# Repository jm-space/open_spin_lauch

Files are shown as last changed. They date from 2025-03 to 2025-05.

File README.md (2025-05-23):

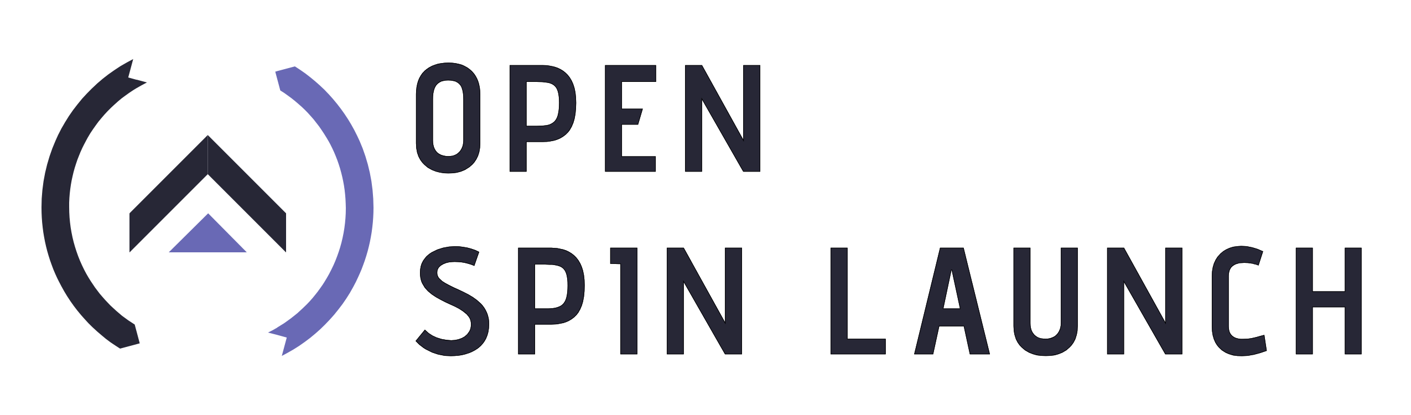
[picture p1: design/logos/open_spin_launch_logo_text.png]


------------------------------------------------

A spin launch system that will be used as the launch platform for many of our future projects. Probable missions that could be conducted with this launch platform include

- Deploy and propulsive landing
- Deploy and in-flight stage ignition
- Deploy to UAV flight transition

The system's main objective is to support the goal of a propulsive landing by accurately deploying it to a target altitude. 

## Requirements

### Spin Launcher

- Maximum achievable altitude: 150 m (theoretical altitude - drag not included)
- Maximum radius: 2 m
- Maximum rocket weight: 2 kg
- Spin up mechanism: 
the contraption should be built in a way so that it can either be spun up  (i) manually with human power through cycling or (ii) with the help of an asynchronous electric motor. 
For human cycling power, a maximum of 800 W is assumed for a maximum duration of 30 s.
- Spin-up retrofit: initially method (i) will be installed. However, method (ii) should be easily installable without any changes. In addition, a clutch should allow for seamless switching between the two modes. 
- Release mechanism: (i) must be able to release two attachment points at specific times, (ii) the release mechanism must be able to deploy the vehicle with a directional accuracy of 1°, which results in a landing zone deviation of +-10 m when launched to the absolute maximum altitude of 150 m with target direction 3°. (iii) The timing accuracy of the differential release mechanism must be high enough, such that if a remaining rotation is induced by the inaccuracy of the differential release, the fins are able to keep the altitude loss and trajectory deviation sufficiently small. 
- Counterweight: instead of utilizing a counterweight, a second (decoy) rocket should be attached that will be released in the same launch direction with a time offset of half a rotation. The axle should be able to withstand the half-rotation induced imbalance. 
- Frame structure: will be made of rectangular steel tubes that will be connected by welding.
- Movability: the contraption should be built on a movable platform for easy commuting. In addition, the platform could be powered by the integrated cycle.  
- Modularity: the individual components of the spin launcher should be split into modules to allow for easy replacements and upgrades. In addition, the entire spin launch system should be able to be retrofitted into a bus without much additional effort. 
- Video coverage: a camera should be installed in the spin launcher's arm so that it can capture the differential release of the vehicle. 

### Rocket

Requirements and expected feature changes:

- Structural integrity: the rocket must be able to withstand the highest occurring launch g-forces. 
- Attachment points: the rocket should integrate two attachment points with which it can be connected to the spin launcher. Those attachment points should be high-strength, durable, and should allow for rapid reuse. 
- Fins and COG: the rocket will have the landing engines and most of its weight in its front and fins in its rear, which allow for a passively stabilized launch. After reaching apogee, the rocket will flip into its stable descent orientation, with its fins being on top and the engine pointing downwards. 
- Thrust vector control: (i) the new TVC system should use off-the shelf gears for higher precision. (ii) it should utilize KST servos for faster actuation speeds and higher accuracy. (iii) and it should be available in two configurations - one for our self-developed solid rocket engines and one for a set of up to five Klima Raketenmodellbau engines. (iv) a life thrust measuring system should be incorporated into the new TVC system. 
- Solid rocket engines: over the course of this vehicle's development several types of engines should be devised: (i) a long-burning engine primarily used for landing maneuvers (ii) a high thrust engine for in-flight ignition, and (iii) a long burn time medium thrust version for rocket powered UAV flight.  
- Throttle mechanism: some mechanism should be devise that allows for sufficient throttle control to increase the likelihood of a successful landing. 
- GNSS receiver: for position and velocity determination a RTK GNSS receiver should be incorporated. 
- Video coverage: two cameras should be installed in the vehicle - one that is directed towards the TVC system and one that is filming the vehicle's exterior.

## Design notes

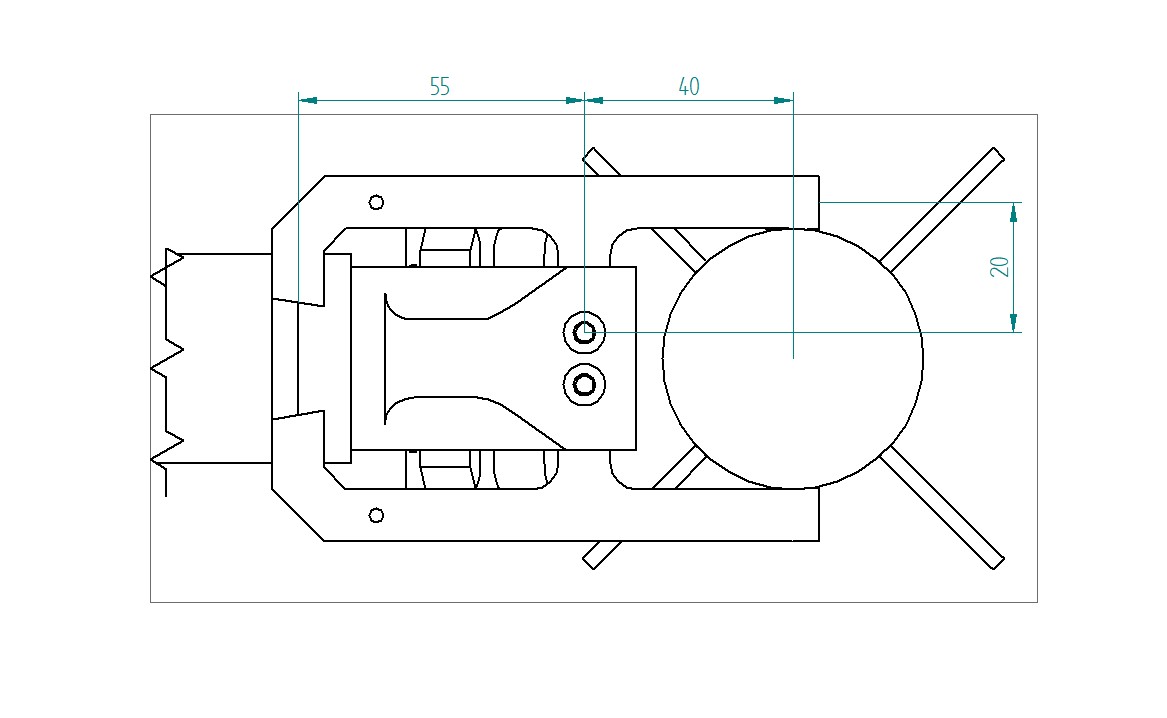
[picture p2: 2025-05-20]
documents/calculations/FBD1-clamp.jpg

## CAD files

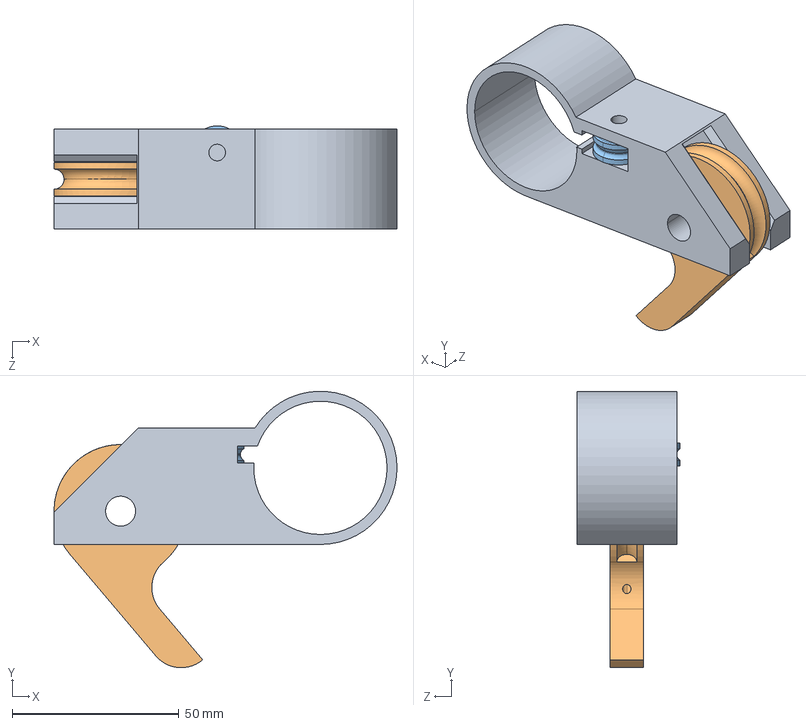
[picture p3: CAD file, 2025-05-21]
construction/prototype_v2/main_trigger.STEP
103.0 x 83.0 x 31.0 mm
housing
lever

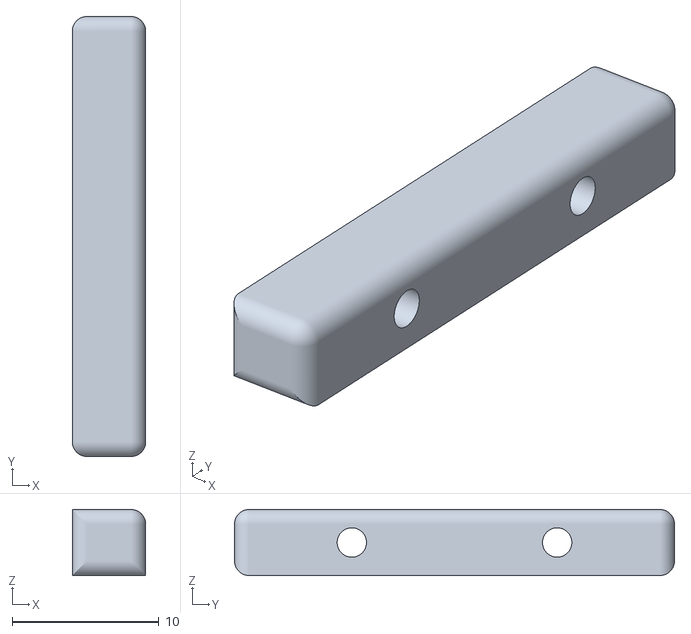
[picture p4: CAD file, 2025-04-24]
construction/small-scale_prototype/a1_front_release_mechanism/stl/upper_clamp_release_pin.stl
5.00 x 30.0 x 4.50

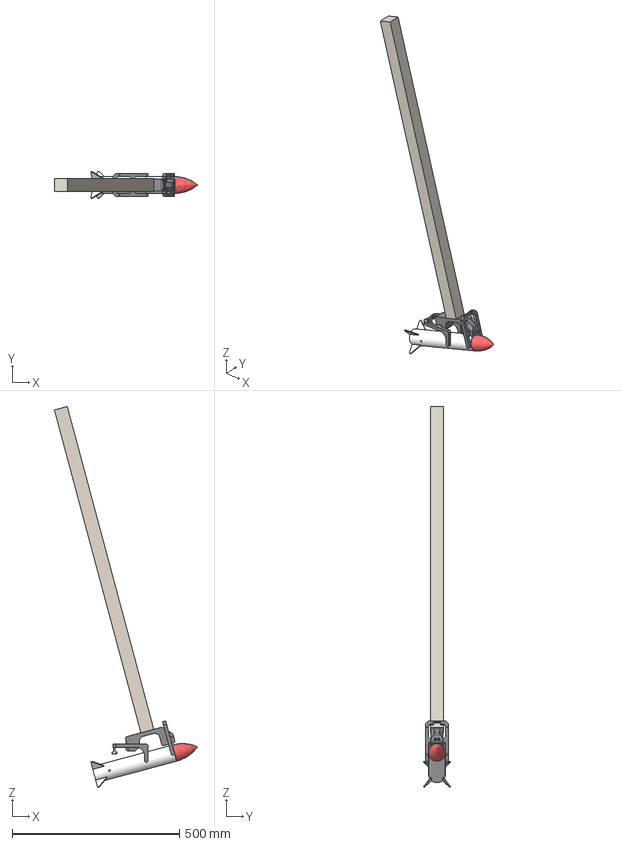
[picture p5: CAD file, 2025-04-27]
construction/small-scale_prototype/a2_auto_release_mechanism/a2_release_mechanism.stp
428.6 x 81.0 x 1140.0 mm
rod_endpart
rocket_dummy
upper_rocket_clamp_left
a1_upper_rocket_clamp_left
upper_rocket_clamp_right
a1_upper_rocket_clamp_right
upper_clamp_release_pin
a1_upper_clamp_release_pin
rocket_dummy_nose_cone
attachment_wood_plank

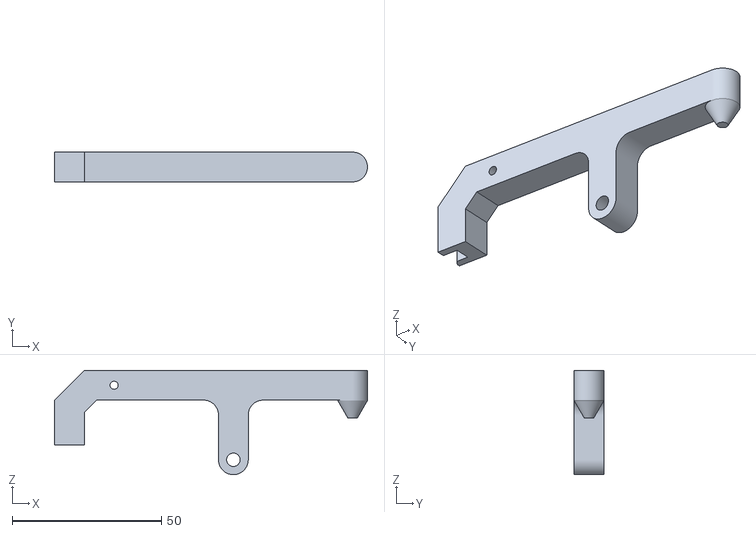
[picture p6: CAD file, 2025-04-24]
construction/small-scale_prototype/a2_auto_release_mechanism/stl/upper_rocket_clamp_left.stl
105.0 x 10.0 x 35.0

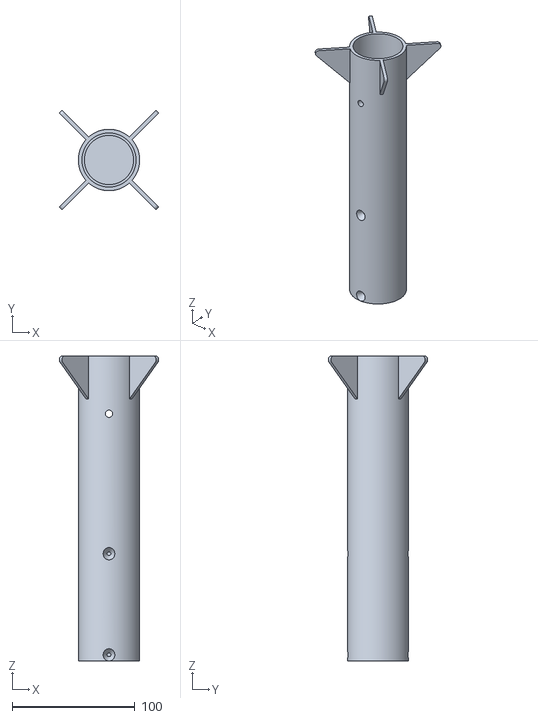
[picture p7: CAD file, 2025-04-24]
construction/small-scale_prototype/a2_auto_release_mechanism/stl_2/rocket_dummy.stl
81.0 x 81.0 x 248.3

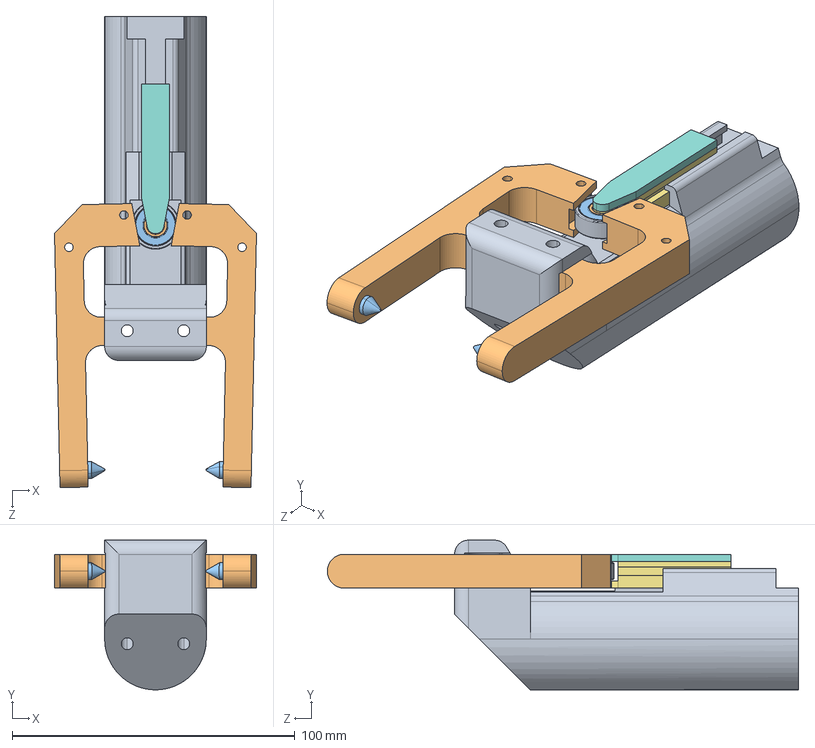
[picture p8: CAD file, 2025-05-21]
construction/prototype_v2/front_release.STEP
71.5 x 53.0 x 166.8 mm
front_endpart
front_clamp_left_b x 2
din8012 x 2
skf_bearing_hk_0306_tn_2_01 x 2
skf_bearing_hk_0306_tn_2_02 x 2
skf_bearing_hk_0306_tn_2_03 x 2
release_pin_lower
release_pin_upper
w_606-2rs1_01
w_606-2rs1_02
w_606-2rs1_03
w_606-2rs1_04
w_606-2rs1_05

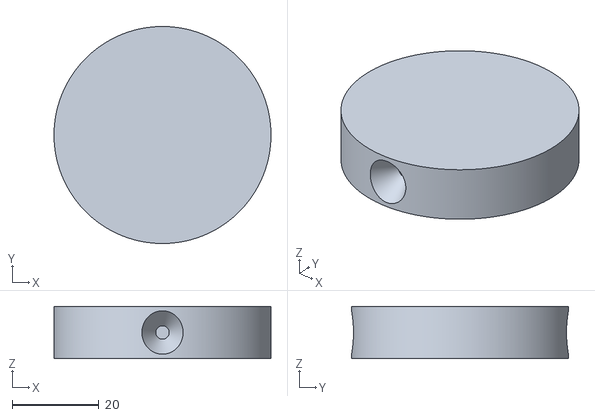
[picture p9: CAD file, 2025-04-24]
construction/small-scale_prototype/a2_auto_release_mechanism/stl/rocket_dummy.stl
50.0 x 50.0 x 12.0

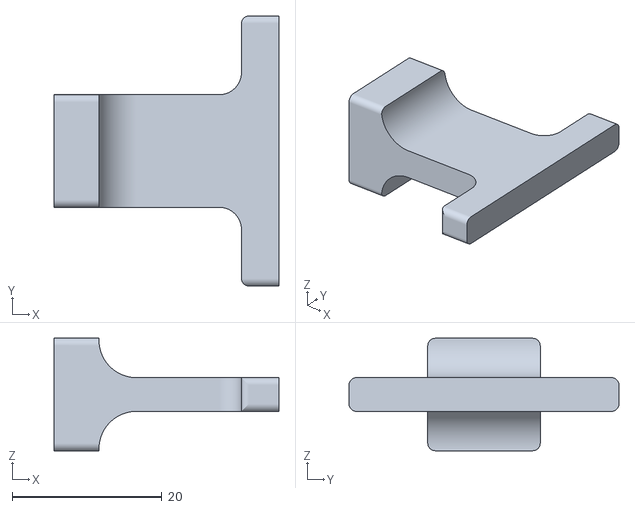
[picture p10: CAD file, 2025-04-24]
construction/small-scale_prototype/a2_auto_release_mechanism/stl_2/upper_clamp_release_pin.stl
30.0 x 36.0 x 15.0

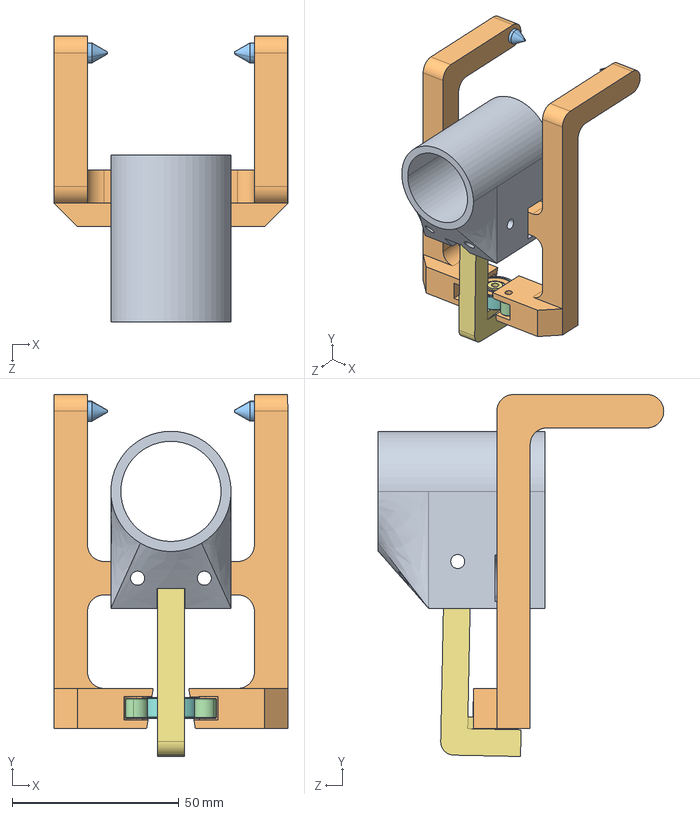
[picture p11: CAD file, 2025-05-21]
construction/prototype_v2/rear_release.STEP
70.0 x 108.4 x 85.5 mm
rear_endpart
rear_clamp_left_b
din8012 x 2
skf_bearing_hk_0306_tn_2_01 x 2
skf_bearing_hk_0306_tn_2_02 x 2
skf_bearing_hk_0306_tn_2_03 x 2
rear_clamp_right_b
swing_b
w_606-2rs1_01
w_606-2rs1_02
w_606-2rs1_03
w_606-2rs1_04
w_606-2rs1_05

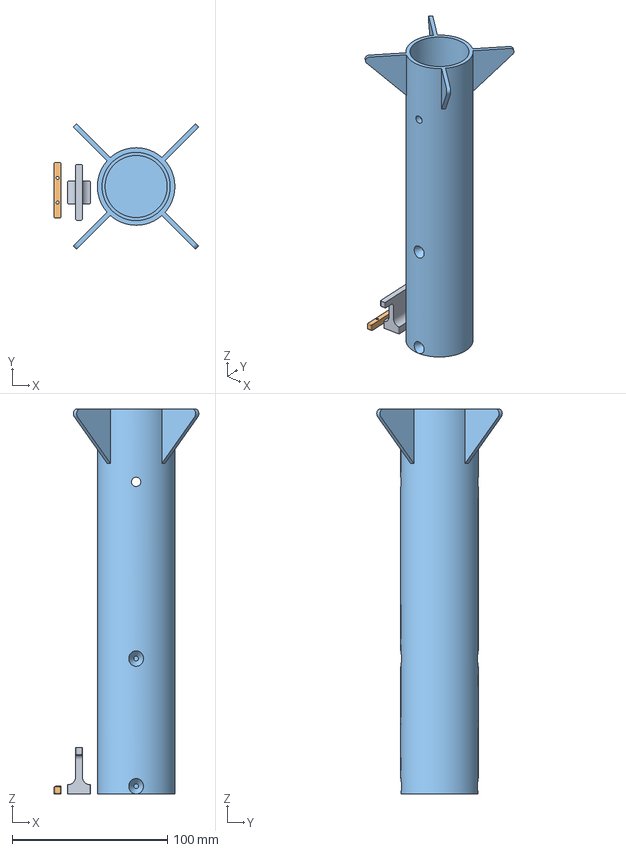
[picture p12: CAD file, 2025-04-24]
construction/small-scale_prototype/a2_auto_release_mechanism/stl_2/a1_upper_clamp_release_pin.3mf
93.4 x 81.0 x 248.4 mm
upper_clamp_release_pin.stl
a1_upper_clamp_release_pin.stl
rocket_dummy.stl

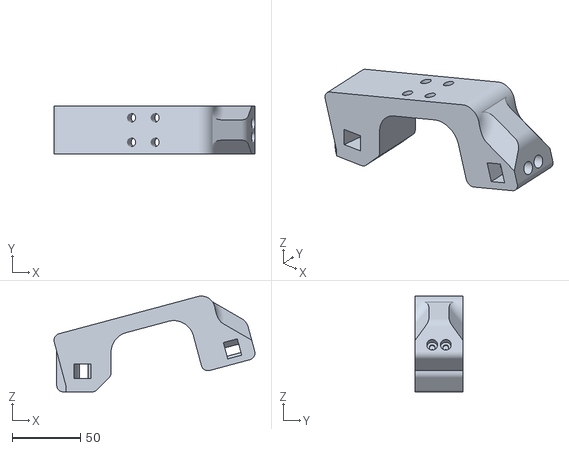
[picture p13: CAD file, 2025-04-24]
construction/small-scale_prototype/a2_auto_release_mechanism/stl_2/rod_endpart.stl
147.7 x 35.0 x 70.4

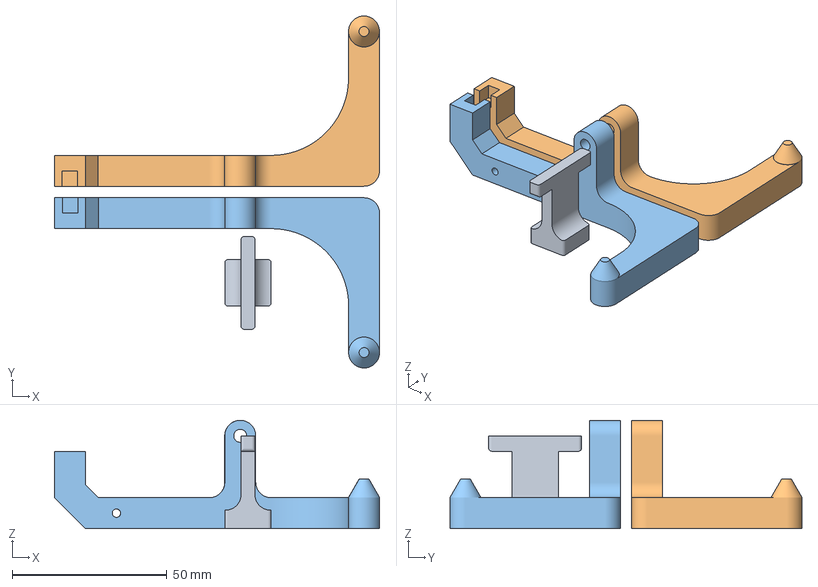
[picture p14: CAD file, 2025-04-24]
construction/small-scale_prototype/a2_auto_release_mechanism/stl_2/upper_rocket_clamp_left.3mf
105.0 x 113.7 x 35.0 mm
upper_clamp_release_pin.stl
upper_rocket_clamp_left.stl
upper_rocket_clamp_right.stl

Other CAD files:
construction/small-scale_prototype/a1_front_release_mechanism/stl/upper_rocket_clamp_right.stl
construction/small-scale_prototype/a2_auto_release_mechanism/stl/upper_rocket_clamp_right.stl
construction/small-scale_prototype/a2_auto_release_mechanism/stl_2/a1_upper_rocket_clamp_right.stl
construction/small-scale_prototype/a2_auto_release_mechanism/stl_2/a1_upper_clamp_release_pin.stl
construction/small-scale_prototype/a2_auto_release_mechanism/stl_2/a1_upper_rocket_clamp_left.stl
construction/small-scale_prototype/a2_auto_release_mechanism/stl_2/rocket_dummy_nose_cone.3mf
construction/small-scale_prototype/a2_auto_release_mechanism/stl_2/upper_rocket_clamp_left.stl
construction/small-scale_prototype/a2_auto_release_mechanism/stl_2/upper_rocket_clamp_right.stl

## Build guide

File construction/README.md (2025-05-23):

# Construction

For testing purposes, a small scale prototype was built with special focus on the release mechanism

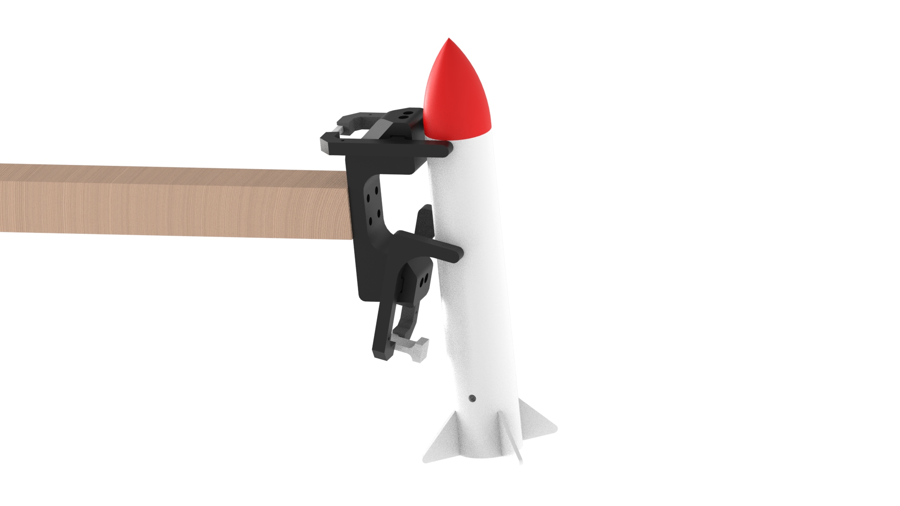
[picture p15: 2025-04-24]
construction/small-scale_prototype/a2_auto_release_mechanism/small_scale_release_prototype.jpg

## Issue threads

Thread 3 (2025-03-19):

CAD & Parts Sourcing of Full Scale Spin Launch System

moserjoki, 2025-03-19:
- Iterate on the release mechanism based on the prototype
- Calculate all critical components and document those calculations
- Integrate the spin launcher into a metal frame that will be welded
- Order necessary components to allow for an assembly start at the beginning of July

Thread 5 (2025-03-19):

Assemble Full Scale Spin Launcher

moserjoki, 2025-03-19:
- Assemble full scale spin launcher
- Includes:
- Welding of frame structure
- Integration of bike spin up mechanism
- Assembly of release mechanism
- Assembly of Rocket release dummy

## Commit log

2025-03-16 Added initial calculation Excel document to the public repo
    [Spin Launch - Master Calculations.xlsx]
2025-03-18 Created first steps towards a small scale prototype, which will be intended to test the functionality of the release mechanism
    [62599720.cfg, a_small-scale_prototype.cfg, n1_ball_pillow_block_bearing_d20_b20.cfg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]
2025-03-29 start of center bearing calculation
    [Spin Launch - Master Calculations.xlsx]
2025-03-29 Added release mechanism to release prototype CAD
    [a1_release_mechanism.cfg, a_small-scale_prototype.cfg]
2025-04-14 creating branch and allocating names
    [a1_center_bearing.cfg, a_main_spin_launcher.cfg]
2025-04-18 Added quick release on release plate
    [a_small-scale_prototype.cfg]
2025-04-24 Double Release Prototype
    [Spin Launch - Master Calculations.xlsx, a1_release_mechanism.cfg, a1_upper_clamp_release_pin.3mf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]
2025-04-25 Added macro-enabled excel for drag-aware trajectory calculation
    [Spin Launch - Master Calculations - Macro.xlsm]
2025-04-27 Added step files for easy access from other CAD design softwares
    [a2_release_mechanism.cfg, a2_release_mechanism.stp]
2025-05-13 Update of calculation tool with first GUI
    [Spin Launch - Master Calculations - Macro.xlsm, a2_release_mechanism.cfg]
2025-05-20 Clamp Calculation and Structural Object Update
    [Spin Launch - Master Calculations - Macro.xlsm, a2_release_mechanism.cfg, reinforced_clamp_for_fea.cfg]
2025-05-20 Create Prototype V2
2025-05-20 Prototype V2 Assemblies
    [front_release.STEP, main_trigger.STEP, rear_release.STEP]
2025-05-21 rework of core to bigger diameter and 30x30 beam
    [a1_center_bearing.cfg, a_main_spin_launcher.cfg]
2025-05-22 center bearing version 0.1.0
    [a1_center_bearing.cfg, n1_[6014].cfg]
2025-05-22 reverting logo
    [a1_center_bearing.cfg]
2025-05-23 Clamp Reinforced with metallic Insert
    [front_release.cfg]
